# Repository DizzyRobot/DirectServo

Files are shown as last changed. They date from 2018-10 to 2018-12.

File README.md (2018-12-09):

# DirectServo
Controller that drives BLDC motor as servo

More details to come, 
for now this is just a placeholder informing that this is a motor driver microcontroller board that can be attached to a 3-phase
BLDC motor (such as a camera gimbal) and control it via RS485 protocol. 
It receives torque commands and sends back the angular position read via magnetic sensor.

[https://www.dizzy.ai/documentation/motor-driver/]

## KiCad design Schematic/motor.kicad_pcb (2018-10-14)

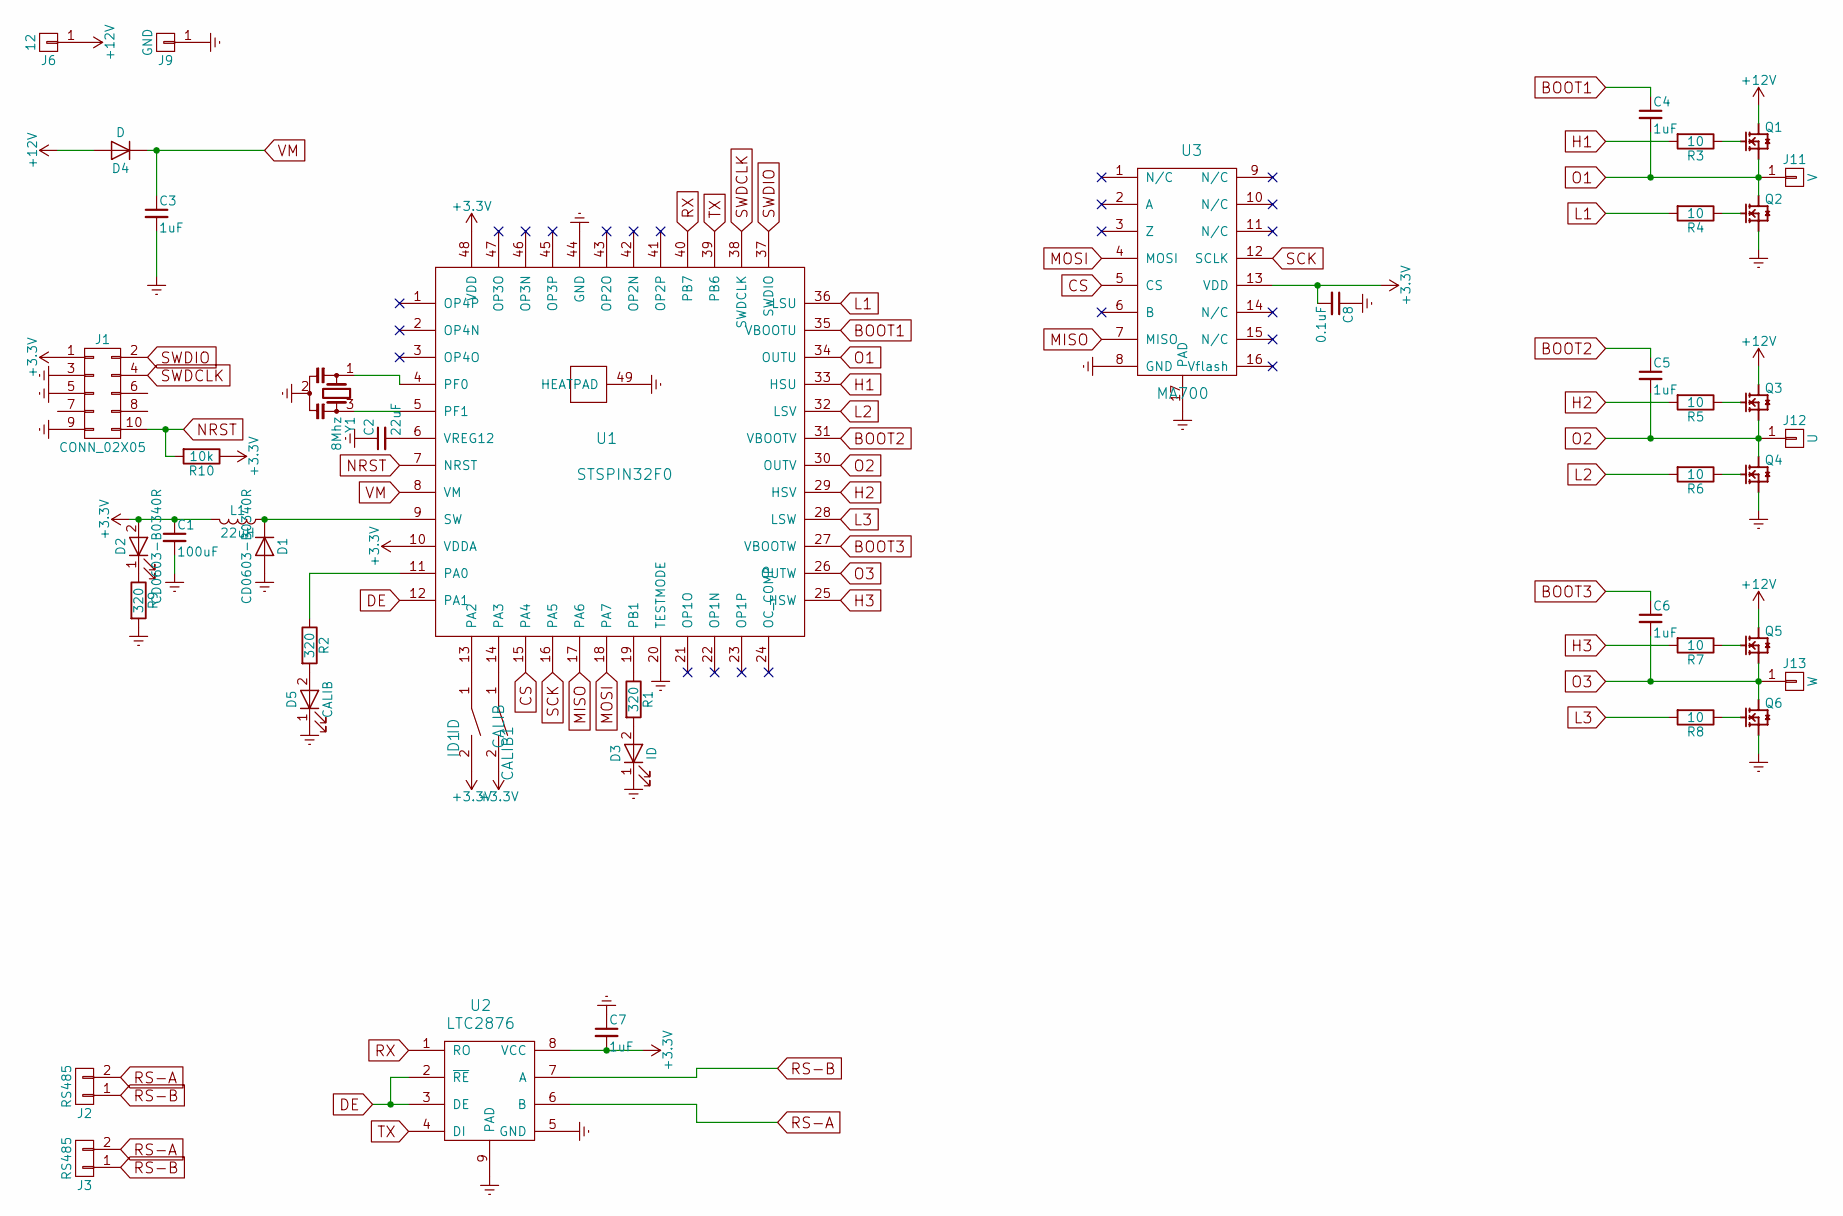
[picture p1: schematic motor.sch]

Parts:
C1: 100uF; C_0805
C2: 22uF; C_0805
C3: 1uF; C_1206
C4, C5, C6, C7: 1uF; C_0603
C8: 0.1uF; C_0603
CALIB1: CALIB; R_1206
D1: CD0603-B0340R; D_SOD-323F
D2: CD0603-B0340R; LED_0603
D3: ID; LED_0603
D4: D; D_SOD-323F
D5: CALIB; LED_0603
ID1: ID; R_1206
J1: CONN_02X05; Pin_Header_Straight_2x05_Pitch1.27mm_SMD
J2, J3: RS485; Pin_Header_Straight_1x02_Pitch2.54mm
J6: 12; Pin_Header_Straight_1x01_Pitch2.54mm
J9: GND; Pin_Header_Straight_1x01_Pitch2.54mm
J11: V; Pin_Header_Straight_1x01_Pitch2.54mm
J12: U; Pin_Header_Straight_1x01_Pitch2.54mm
J13: W; Pin_Header_Straight_1x01_Pitch2.54mm
L1: 22uH; L_1210
Q1, Q3, Q5: PSMN3R3-40YS
Q2, Q4, Q6: PSMN3R3-40YS; PSMN3R3-40YS-vias
R1, R2, R9: 320; R_0603
R3, R4, R5, R6, R7, R8: 10; R_0603
R10: 10k; R_0603
U1: STSPIN32F0; STSPIN32-nopad
U2: LTC2876
U3: MA700; QFN-16-1EP_3x3mm_Pitch0.5mm
Y1: 8Mhz; Oscillator

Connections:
+3V3: C1.1, C7.2, C8.2, CALIB1.2, D2.2 (A), ID1.2, J1.1, L1.2, R10.1, U1.10 (VDDA), U1.48 (VDD), U2.8 (VCC), U3.13 (VDD)
+12V: D4.2 (A), J6.1, Q1.5678 (D), Q3.5678 (D), Q5.5678 (D)
BOOT1: C4.1, U1.35 (VBOOTU)
BOOT2: C5.1, U1.31 (VBOOTV)
BOOT3: C6.1, U1.27 (VBOOTW)
CS: U1.15 (PA4), U3.5 (CS)
DE: U1.12 (PA1), U2.2 (~RE), U2.3 (DE)
Earth: C1.2, C2.1, C3.2, C7.1, C8.1, D1.2 (A), D3.1 (K), D5.1 (K), J1.3, J1.5, J1.9, J9.1, Q2.1 (S), Q2.2 (S), Q2.3 (S), Q4.1 (S), Q4.2 (S), Q4.3 (S), Q6.1 (S), Q6.2 (S), Q6.3 (S), R9.2, U1.20 (TESTMODE), U1.44 (GND), U1.49 (HEATPAD), U2.5 (GND), U2.9 (PAD), U3.8 (GND), U3.17 (PAD), Y1.2
H1: R3.2, U1.33 (HSU)
H2: R5.2, U1.29 (HSV)
H3: R7.2, U1.25 (HSW)
L1: R4.2, U1.36 (LSU)
L2: R6.2, U1.32 (LSV)
L3: R8.2, U1.28 (LSW)
MISO: U1.17 (PA6), U3.7 (MISO)
MOSI: U1.18 (PA7), U3.4 (MOSI)
NRST: J1.10, R10.2, U1.7 (NRST)
unnamed: C2.2, U1.6 (VREG12)
unnamed: CALIB1.1, U1.14 (PA3)
unnamed: D1.1 (K), L1.1, U1.9 (SW)
unnamed: D2.1 (K), R9.1
unnamed: D3.2 (A), R1.2
unnamed: D5.2 (A), R2.2
unnamed: ID1.1, U1.13 (PA2)
unnamed: Q1.4 (G), R3.1
unnamed: Q2.4 (G), R4.1
unnamed: Q3.4 (G), R5.1
unnamed: Q4.4 (G), R6.1
unnamed: Q5.4 (G), R7.1
unnamed: Q6.4 (G), R8.1
unnamed: R1.1, U1.19 (PB1)
unnamed: R2.1, U1.11 (PA0)
unnamed: U1.4 (PF0), Y1.1
unnamed: U1.5 (PF1), Y1.3
O1: C4.2, J11.1, Q1.1 (S), Q1.2 (S), Q1.3 (S), Q2.5678 (D), U1.34 (OUTU)
O2: C5.2, J12.1, Q3.1 (S), Q3.2 (S), Q3.3 (S), Q4.5678 (D), U1.30 (OUTV)
O3: C6.2, J13.1, Q5.1 (S), Q5.2 (S), Q5.3 (S), Q6.5678 (D), U1.26 (OUTW)
RS-A: J2.2, J3.2, U2.6 (B)
RS-B: J2.1, J3.1, U2.7 (A)
RX: U1.40 (PB7), U2.1 (RO)
SCK: U1.16 (PA5), U3.12 (SCLK)
SWDCLK: J1.4, U1.38 (SWDCLK)
SWDIO: J1.2, U1.37 (SWDIO)
TX: U1.39 (PB6), U2.4 (DI)
VM: C3.1, D4.1 (K), U1.8 (VM)

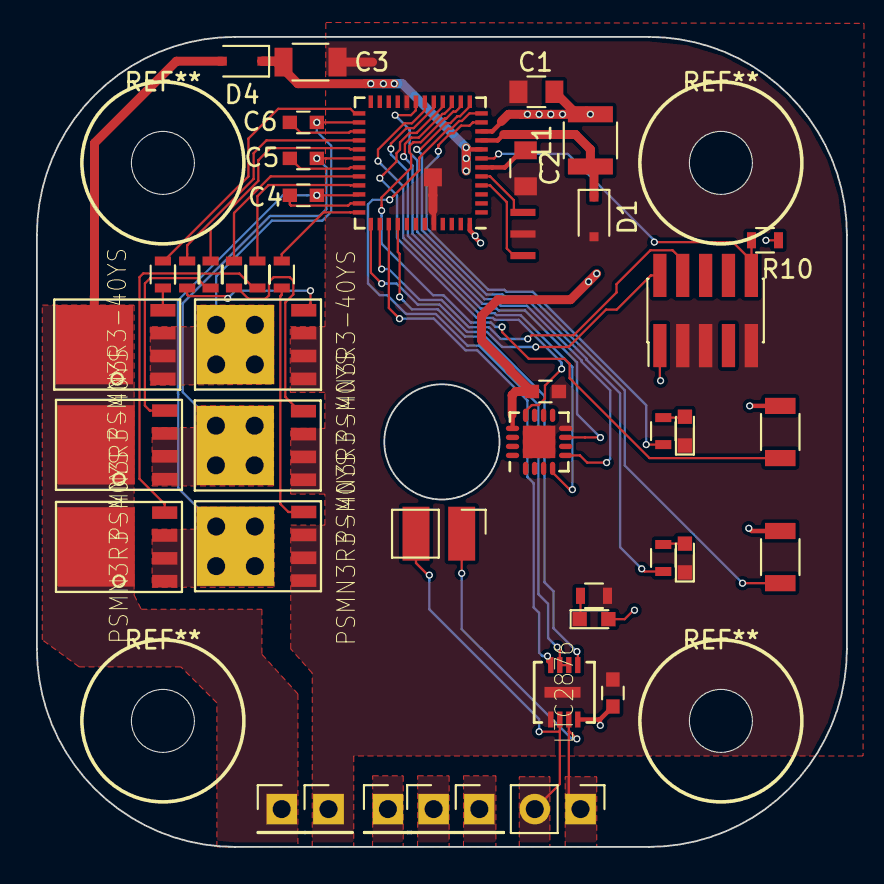
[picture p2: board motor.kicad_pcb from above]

Board: 2 copper layers, 45.0 x 45.0 mm, 44 parts (0 on the bottom side), 45 nets.

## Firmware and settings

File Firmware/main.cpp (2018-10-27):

#include <main.h>

int ensureConfigured() {
	bool calibConfigured = config->calibrated;
	bool idConfigured = config->controllerId != 0 && config->controllerId != -1;
	
	if (!calibConfigured) blinkCalib(true);
	if (!idConfigured) blinkId(true);
}

//

int main(void) {
	initClockExternal();
	initButtons();
	initUsart();
	initSpi();
	initSysTick();
	//delay(100);
	initPwm();
	
	//calibrate();
	delay(2000);
	
	ensureConfigured();
	
	//usartTorqueCommandValue = -250;	
	
	usartDmaSendRequested = false;
	buttonIdPressed = false;
	buttonCalibPressed = false;

	while (true){
		spiReadAngleFiltered();
		setPwmTorque();
		
		if (usartDmaSendRequested && !usartDmaSendBusy)
		{
			usartSendAngle();
			usartDmaSendRequested = false;
		}
		
		if (usartCommandReceived)
		{
			processUsartCommand();
			usartCommandReceived = false;
		}
		
		if (buttonIdPressed)
		{
			incrementIdAndSave();
			buttonIdPressed = false;
		}
		
		if (buttonCalibPressed)
		{
			calibrate(); 
			buttonCalibPressed = false;
			usartTorqueCommandValue = 0;
			usartDmaSendRequested = false;
		}
	}
}

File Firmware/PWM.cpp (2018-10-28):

#include <main.h>

const int timer_scale = 7;
const int sin_zero = sin_range / 2;
const int phase2 = sin_period / 3;
const int phase3 = sin_period * 2 / 3;
const int ninetyDeg = sin_period / 4;

/// A sine approximation via a third-order approx.
/// @param x    Angle (with 2^15 units/circle)
/// @return     Sine value (Q12)
int isin_S3(int x)
{
    // S(x) = x * ( (3<<p) - (x*x>>r) ) >> s
    // n : Q-pos for quarter circle             13
    // A : Q-pos for output                     12
    // p : Q-pos for parentheses intermediate   15
    // r = 2n-p                                 11
    // s = A-1-p-n                              17

	static const int qN = 13, qA = 12, qP = 15, qR = 2*qN - qP, qS = qN + qP + 1 - qA;

	x = x << (30 - qN);          // shift to full s32 range (Q13->Q30)

	if ((x ^ (x << 1)) < 0)     // test for quadrant 1 or 2
		x = (1 << 31) - x;

	x = x >> (30 - qN);

	return x * ((3 << qP) - (x*x >> qR)) >> qS;
}

void initPwm() {
	TIM1->ARR = sin_range / timer_scale;							// tim1 period, about 20kHz

	// tim1 config channel

	TIM1->CCMR1 |= TIM_CCMR1_OC1PE |					// Output compare on channel 1 preload enable (for pin B-13, low-side 1)
		           (0x06 << TIM_CCMR1_OC1M_Pos) |		// Output compare on channel 1 mode = 110 (PWM mode 1)
				   TIM_CCMR1_OC2PE |					// Output compare on channel 2 preload enable (for pin B-14, low-side 2)
		           (0x06 << TIM_CCMR1_OC2M_Pos);		// Output compare on channel 2 mode = 110 (PWM mode 1)
	
	TIM1->CCMR2 |= TIM_CCMR2_OC3PE |					// Output compare channel 3 preload enable (for pin A-10, high-side and pin B-15, low-side)
 			       (0x06 << TIM_CCMR2_OC3M_Pos);		// Output compare 3 mode = 110 (PWM mode 1)
	
	// GPIOA
	
	GPIOA->MODER |= (0x02 << GPIO_MODER_MODER8_Pos) |	// alternative function for pin A-8 (pwm channel 1, positive)
					(0x02 << GPIO_MODER_MODER9_Pos) |	// alternative function for pin A-9 (pwm channel 2, positive)
				    (0x02 << GPIO_MODER_MODER10_Pos) |	// alternative function for pin A-10 (pwm channel 3, positive)
		
					(0x01 << GPIO_MODER_MODER11_Pos);	// output for pin A-11 (overcurrent control)
	
	GPIOA->OSPEEDR |= GPIO_OSPEEDR_OSPEEDR8 |			// high speed for pin A-8 (pwm channel 1, positive)
				      GPIO_OSPEEDR_OSPEEDR9 |			// high speed for pin A-9 (pwm channel 2, positive)
		              GPIO_OSPEEDR_OSPEEDR10 |			// high speed for pin A-10 (pwm channel 3, positive)
		
					  (0x01 << GPIO_OSPEEDR_OSPEEDR11_Pos);	// medium speed for pin A-11 (overcurrent control)
	
	GPIOA->AFR[1] |= (0x02 << GPIO_AFRH_AFSEL8_Pos) |	// for pin A-8 alternative funciton 2
					 (0x02 << GPIO_AFRH_AFSEL9_Pos) |	// for pin A-9 alternative funciton 2
					 (0x02 << GPIO_AFRH_AFSEL10_Pos);	// for pin A-10 alternative funciton 2
	
	GPIOA->PUPDR |= (0x01 << GPIO_PUPDR_PUPDR11_Pos);	// pull-up for pin A-11 (overcurrent control)
	
	// GPIOB
	
	GPIOB->MODER |= (0x02 << GPIO_MODER_MODER13_Pos) |	// alternate function for pin B-13 (PWM channel 1, negative)
		            (0x02 << GPIO_MODER_MODER14_Pos) |	// alternate function for pin B-14 (PWM channel 2, negative)
		            (0x02 << GPIO_MODER_MODER15_Pos);	// alternate function for pin B-15 (PWM channel 3, negative)
	
	GPIOB->OSPEEDR |= GPIO_OSPEEDR_OSPEEDR13 |			// high speed for pin B-13 (pwm channel 1, negative)
		              GPIO_OSPEEDR_OSPEEDR14 |			// high speed for pin B-14 (pwm channel 2, negative)
		              GPIO_OSPEEDR_OSPEEDR15;			// high speed for pin B-15 (pwm channel 3, negative)
	
	GPIOB->AFR[1] |= (0x02 << GPIO_AFRH_AFSEL13_Pos) |	// for pin B-13 alternative funciton 2
		             (0x02 << GPIO_AFRH_AFSEL14_Pos) |	// for pin B-14 alternative funciton 2
	                 (0x02 << GPIO_AFRH_AFSEL15_Pos);	// for pin B-15 alternative funciton 2
	
	//
	
	TIM1->CR1 |= (0x01 << TIM_CR1_CMS_Pos);				// center-aligned mode 1 - up&down
	
	TIM1->RCR = 0x1;									// repetition counter
	
	TIM1->BDTR |= TIM_BDTR_MOE |						// main output enable
		          TIM_BDTR_OSSR |						// Off-state selection for Run mode
				  TIM_BDTR_OSSI |						// Off-state selection for Idle mode
		          0x30;									// dead-time = 1uS, 48 counts
	
	TIM1->CR1 |= TIM_AUTORELOAD_PRELOAD_ENABLE;			// enable timer 1
	
	TIM1->CCER |= TIM_CCER_CC1E |						// enable channel1, positive
			      TIM_CCER_CC2E |						// enable channel2, positive
		          TIM_CCER_CC3E |						// enable channel3, positive
		
		          TIM_CCER_CC1NE |						// enable channel 1, negative
		          TIM_CCER_CC2NE |						// enable channel 2, negative
		          TIM_CCER_CC3NE;						// enable channel 3, negative

	TIM1->CCR1 = 0;										// zero duty-cycle on all channels
	TIM1->CCR2 = 0;
	TIM1->CCR3 = 0;
	
	TIM1->CR1 |= TIM_CR1_CEN;							// enable timer 1
	
	// GPIOF - turn MOSFET driver on
	
	GPIOF->MODER |= (0x01 << GPIO_MODER_MODER6_Pos) |	// output mode for pin F-6 (standby mode)
		            (0x01 << GPIO_MODER_MODER7_Pos);	// output mode for pin F-7 (standby mode)
	
	GPIOF->PUPDR |= (0x01 << GPIO_PUPDR_PUPDR6_Pos) |	// pull-up for pin F-6
			        (0x01 << GPIO_PUPDR_PUPDR7_Pos);	// pull-up for pin F-7
	
	// over-current config (pin A-11)

	GPIOA->BRR = (1 << 11);								// reset pin 11 (overcurrent does not effect gate driver directly)
	GPIOF->BSRR = (1 << 7);								// disable stand-by mode	
}
void setPwm(int angle, int power) {
//	angle = POSITIVE_MODULO(angle, sin_period);
//	
//	int a1 = angle;
//	int a2 = POSITIVE_MODULO((angle + phase2), sin_period);
//	int a3 = POSITIVE_MODULO((angle + phase3), sin_period);
	
	int a1 = angle % sin_period;
	int a2 = (angle + phase2) % sin_period;
	int a3 = (angle + phase3) % sin_period;
	
	if (a1 < 0) a1 += sin_period;
	if (a2 < 0) a2 += sin_period;
	if (a3 < 0) a3 += sin_period;
	
	a1 = isin_S3(a1) + sin_zero;
	a2 = isin_S3(a2) + sin_zero;
	a3 = isin_S3(a3) + sin_zero;
	
	TIM1->CCR1 = a1 * power / sin_range / timer_scale;
	TIM1->CCR2 = a2 * power / sin_range / timer_scale;
	TIM1->CCR3 = a3 * power / sin_range / timer_scale;
}
void setPwmTorque() {
	int a = getElectricDegrees();
	
	if (usartTorqueCommandValue > 0)
	{
		a += ninetyDeg;
		setPwm(a, usartTorqueCommandValue);
	}
	else
	{
		a -= ninetyDeg;
		setPwm(a, -usartTorqueCommandValue);
	}
}

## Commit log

2018-10-14 second commit
    [motor.kicad_pcb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]
2018-10-21 timer and power range fixes
    [motor.xml]
2018-10-27 just started filtering and decided to save :)
2018-10-28 fixed mag sensor pre-scale
    [Calibrate.cpp, PWM.cpp, SpiMA700.cpp]
